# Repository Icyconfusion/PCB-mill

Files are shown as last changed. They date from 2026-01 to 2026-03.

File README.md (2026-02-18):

# PCB-mill
A small cnc machine for milling FR4 pcbs using an arduino UNO. It is also capable of CNC engraving at low Z travels. You could potentially do laser engraving if you added a laser to it.

**Note to reveiwer:** I have exported the assembly as .STEP, but I had trouble so there is a zipped .stl of the assembly just in case the .step doesn't work. Also I am updating my BOM with the current prices (since submission) so it might be slightly different (most are cheaper) from my cart pictures. Thank you :) Also, yes the spindle is the cheapest option (prices are in AUD so 50-60 USD is 75-90 AUD). The spindle I am purchasing also includes PSU.

I created this project as a means to create PCBs quickly at home, removing the time and cost of ordering PCBs online. Now I can make 2 layer PCBs at home on my desk for quick prototyping. It also taught me a few things about routing with power draws. To use the project, you simply stream Gcode to the machine over usb form a computer, and the machine will replicate it.

# **Assembly**


The assembly of the project is made up of a few key components. The idea is a stationary, square base with linear rails making the Y axis. The H frame moves along thiscarrying the X and Z axis. Motion is achieved through leadscrews.

To start assembly, there is the base frame that the whole machine is supported by. 4 2020 300m T slot Aluminium profiles are arranged in a square, with M5 T nuts and 90 degree connectors holding them in place. Two 300mm MGN12 linear rails are attached to the top edge of the profiles using M3 T nuts.


Now onto the H. The H moves back and forth along the linear rails attached before, this is the Y axis. The H moves along the rails by a 3d printed bracket, to attach it to the MGN12H carriage. Use 4 M2 screws to attach each bracket to the carriages, then 4 M5 T nuts to attach profiles to each bracket.





We now have the two pillars of the H. Attach to 2060 profile to the pillars using M5 T nuts and 90 degree connectors. The bottom edge of the 2060 should be roughly 4 cm from the top of the bracket we assembled (Exactness is not needed as Z leveling and the spindle height on the mount will compensate for this). Attach the linear rails as before.


To assemble the gantry, screw on both rear MGN12H carriages, and linear rails. Attach the limit switch and press the bearing into place. Then assemble the spindle plate and slide onto the gantry.




Finally, attach the motor, coupler, nutblock and rod, and then slide onto the H frame. The H frame can now slide onto the base frame rails.



Last steps, attach a bed/spoilboard of wood with M5 T nuts. Screw nutblocks to each Y carriage, then mount all 4 Y axis brackets, and their fixing blocks (plus limit switch on one). Now you can feed the rods through and attach the GT2 gears.


Mount the belt plate, motor and drive gear using M5 T nuts, then attach the pulleys.



Finally, attach the X motor bracket, motor and limit switch. The fixing block attaches to the profile on the other side using the T nuts already installed on it. Now you can feed through the leadscrew and assembly is done.



# **Electronics**
The components required for this project are a PSU, an MCU, a spindle or spindle kit, stepper motors, stepper drivers, and limit switches. For the MCU I decided on an arduino UNO because of its pin availability and GRBL compatibility. To power the UNO, I will use an LM2596 buck converter connected to the VIN pin. The PSU is 24v logic, 200w. Power is introduced to the PCB by screw terminals, and powers the VMOT pin of drivers, and 5v logic through the arduino. The steppers are Nema 17 because of their cheap cost and reliability. Drivers used to control these are A4988, which support 1/16 microstepping (why all MS pins are connected to 5v). The 500w spindle comes as a kit including a mount and dedicated PSU. This kit also has speed control to stop the spindle. I am using standard 3 pin limit switches.

## Schematic

Cirkit designer: https://app.cirkitdesigner.com/project/915723a2-d3f0-4d32-8109-c895c4144bcc


## PCB
The PCB for this project interfaces the power supply, steppers, arduino and endstops. It uses wide traces to deliver power from the PSU screw terminals, and has connectors from leftover pins for future connections.


# **Firmware**
The project uses the GRBL library to command the machine. GRBL is a program that instructs the arduino to respond to G-code, sent by a computer. No modifications to GBRL are required other than tweaking default steps/mm, speed, acceleration etc to the machine. To install, copy the edited firmware folder into Arduino IDE libraries, include it in a sketch, and then flash. **It is installed as a zip.**

# **BOM**

### CAD

|Quantity|Name|Picture|
|---|----|---|
| 1 | Spindle plate |  |
| 1 | Gantry plate |  |
| 1 | X motor bracket |  |
| 2 | Y carriage |  |
| 1 | Y bearing bracket with switch |  |
| 3 | Y bearing bracket |  |
| 1 | Belt plate |  |

### PCB

2 layer PCB that is 127x118mm.


### Parts
3x Nema 17 stepper motor

1x Arduino uno

3x A4988 stepper driver

1x 24v 200w PSU

1x 500w Spindle kit

1x LM2596 Buck converter

3x Limit switch

1x V bit

1x Drill bit

1x End mill

1x Collet

6x 300mm 2020 T slot aluminium profile (can do 4x300mm and 2x 200mm, but 6x300mm ended up being cheaper)

1x 300mm 2060 T slot profile

8x 90 degree connector

42x M5 T nut

42x M5 screw

32x M3 screw

32x M3 T nut

1x 100mm T8x8 Leadscrew

3x 300mm T8x8 leadscrew

2x 100mm MGN12 linear rail (with MGN12H carriage)

4x 300mm MGN12 linear rail (with MGN12H carriage)

4x T8x8 nutblock 2mm pitch

2x 5x8mm shaft coupler

1x 5mm bore GT2 timing gear

2x 8mm bore GT2 timing gear

1x GT2 belt (at least 600mm)

2x Toothed GT2 idle pulley

2x Smooth GT2 idle pulley

4x Leadscrew fixing block

1x 16x8x5 bearing

1x spoilboard (any wooden sheet)

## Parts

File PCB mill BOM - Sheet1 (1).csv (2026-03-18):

Product | Quantity | Description | Supplier | Cost (USD) | Link
Nema 17 | 3 |  | Aliexpress | 27.58 | https://www.aliexpress.com/item/1005008459399126.html?curPageLogUid=vCnLCC6yeYcx
Arduino Uno | 1 |  | Aliexpress | 7.35 | https://www.aliexpress.com/item/1005009166789162.html?curPageLogUid=tjsaISsRPt8N
A4988 | 3 |  | Temu | 6.04 | https://www.temu.com/au/5pcs-a4988-stepper--module-with-heat-sink-compatible-for-3d-printer-cnc-machine-robotics-heavy-duty-stepper-driver-board-low-voltage-o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
PSU | 1 |  | Aliexpress | 19.71 | https://www.aliexpress.com/item/1005008333292020.html?curPageLogUid=3XLdhquhUHAm
Spindle kit | 1 |  | Aliexpress | 57.46 | https://www.aliexpress.com/item/1005010191382404.html?curPageLogUid=LtoxsOxznCte
Buck converter | 1 |  | Aliexpress | 2.75 | https://www.aliexpress.com/item/1005007003796615.html?curPageLogUid=gSlzuXtzWAvK
Limit switch | 3 | I already Have these so do not need funding
Z probe | 1 | Already have this so don't need to purchase
V bit | 1 |  | Aliexpress | 8.24 | https://www.aliexpress.com/item/33058654975.html?curPageLogUid=Qey6XFCZCbFq
Collets | 1 |  | Aliexpress | 5.89 | https://www.aliexpress.com/item/1005007808859713.html?curPageLogUid=pwjcIhmlvNUK
Drill bit | 1 |  | Aliexpress | 3.09 | https://www.aliexpress.com/item/1005004411348630.html?curPageLogUid=OUldsYXfEfkz
End mill | 1 |  | Aliexpress | 1.88 | https://www.aliexpress.com/item/1005003291713022.html?curPageLogUid=ExpGw3ASmdvT
2020 T slot | 6 |  | Temu | 26.04 | https://www.temu.com/au/6pcs-of-300mm-11-8-inch-t-slot-2020-aluminum-profile-extrusion-european-standard-anodized-linear-guide-rail-aluminum-profile-extrusion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
2060 T slot | 1 |  | Aliexpress | 14.02 | https://www.aliexpress.com/item/1005002883217574.html?curPageLogUid=gkx3e2LF0D2x
90 degree bracket | 8 | Already have this so don't need to purchase
M5 T Nuts | 42 |  | Temu | 2.14 | https://www.temu.com/au/50pcs-durable-carbon-steel-t-nuts--m4-m5-sizes-nickel-plated-rust-resistant--for-industrial-aluminum-frame--3d-printers-cnc-routers-id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
M3 T nuts | 32 |  | Temu | 2.67 | https://www.temu.com/au/50pcs-of-2020-series-t-nuts--m4-m5-t-slot-nuts-hammer-fasteners-aluminum-profile-plated-carbon-steel-sliding-t-nuts-g-601099530397912.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
100mm leadscrew | 1 |  | Aliexpress | 3.89 | https://www.aliexpress.com/item/1005006178955178.html?curPageLogUid=c6d8BTDWwVPy
300mm leadscrew | 2 |  | Temu | 11.34 | https://www.temu.com/au/tr8x8-screw-with-t8-nut-trapezoidal-thread-2mm-pitch-4-threads-8mm-suitable-for--axis-of-lcd-dlp-sla-3d-printers-and-cnc-machines-g-60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
300mm leadscrew | 1 |  | Alixpress | 6.92 | https://www.aliexpress.com/item/1005009554037590.html?curPageLogUid=qyEKHqJXyCOE
300mm Linear rail | 4 |  | Aliexpress | 57.75 | https://www.aliexpress.com/item/1000007480470.html?curPageLogUid=xv41WxawscEY
100mm Linear rail | 2 |  | Aliexpress | 17.16 | https://www.aliexpress.com/item/1000007480470.html?curPageLogUid=xv41WxawscEY
Nut block | 4 |  | Aliexpress | 5.88 | https://www.aliexpress.com/item/1005007569770523.html?curPageLogUid=jOi7LGcCxd76
Shaft coupler | 2 |  | Aliexpress | 4.13 | https://www.aliexpress.com/item/1005007287308755.html?curPageLogUid=RoRBVjjHc6Wq
5mm Bore GT2 Drive gear | 1 |  | Aliexpress | 1.34 | https://www.aliexpress.com/item/32781681772.html?curPageLogUid=3ezKj0Eq3S47
8mm bore GT2 drive gear | 2 |  | Aliexpress | 1.3 | https://www.aliexpress.com/item/32781681772.html?curPageLogUid=3ezKj0Eq3S47
GT2 belt | 1 |  | Aliexpress | 1.84 | https://www.aliexpress.com/item/1005003301991078.html?curPageLogUid=Z2PgWSwreJ6X
Gt2 idle pulleys | 4 | 2 with teeth, 2 without | Aliexpress | 4.83 | https://www.aliexpress.com/item/32817328238.html?curPageLogUid=Ry0fcXbuAR7Z
Leadscrew fixing block | 4 |  | Aliexpress | 7.4 | https://www.aliexpress.com/item/1005009834401051.html?curPageLogUid=naPMBq5fiutL
Bearing | 1 |  | Aliexpress | 3.56 | https://www.aliexpress.com/item/1005004937963687.html?curPageLogUid=k503JPjwGYyO
 |  |  |  | 312.2

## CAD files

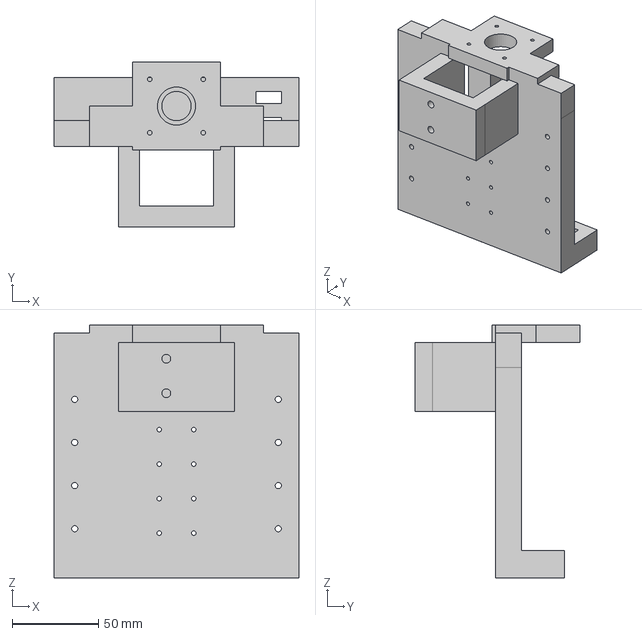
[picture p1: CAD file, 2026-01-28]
CAD/Plate Gantry.step
142.0 x 95.6 x 146.5 mm

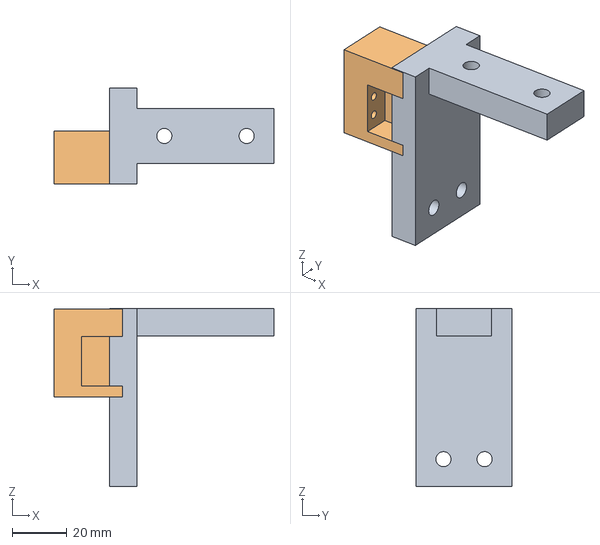
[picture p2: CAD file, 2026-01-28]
CAD/Y bearing bracket with switch.step
80.2 x 35.0 x 65.0 mm

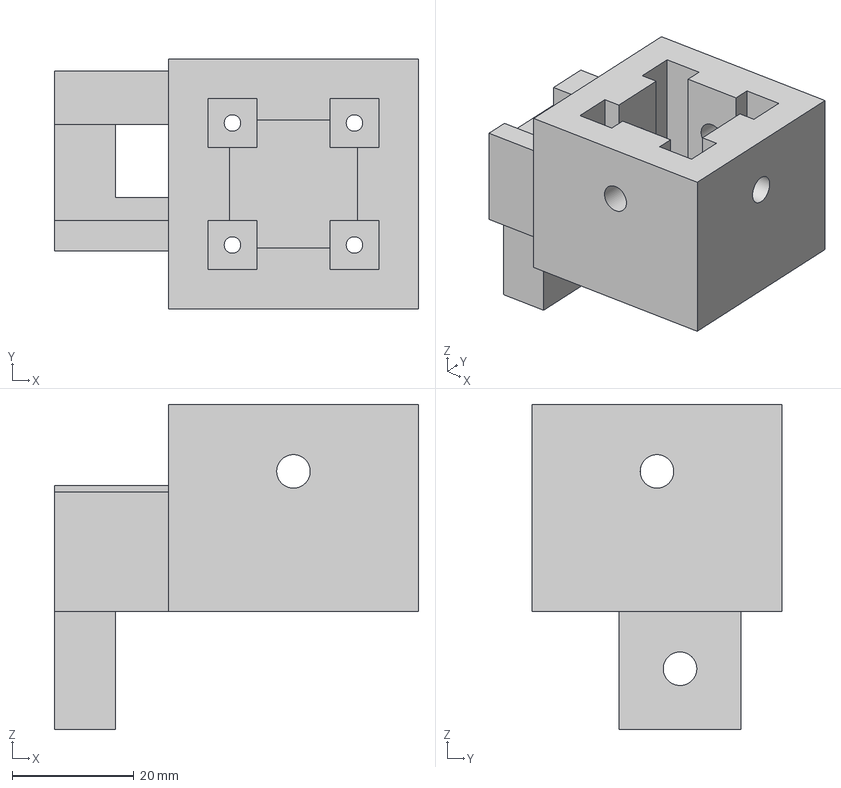
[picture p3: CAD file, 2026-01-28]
CAD/Y carriage.step
59.7 x 41.0 x 53.4 mm

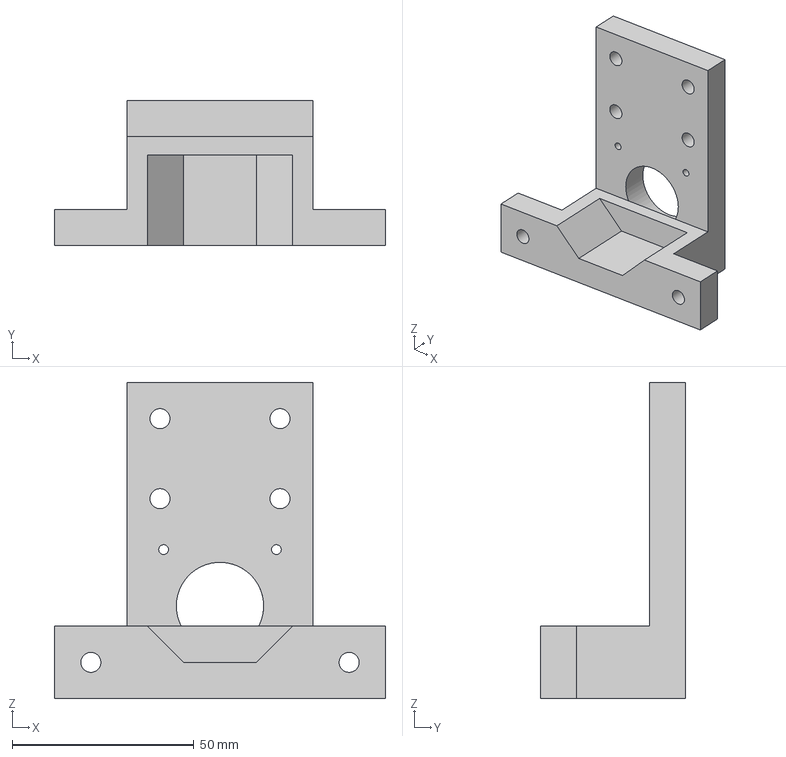
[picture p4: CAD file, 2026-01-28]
CAD/Belt plate.step
91.0 x 40.0 x 87.0 mm

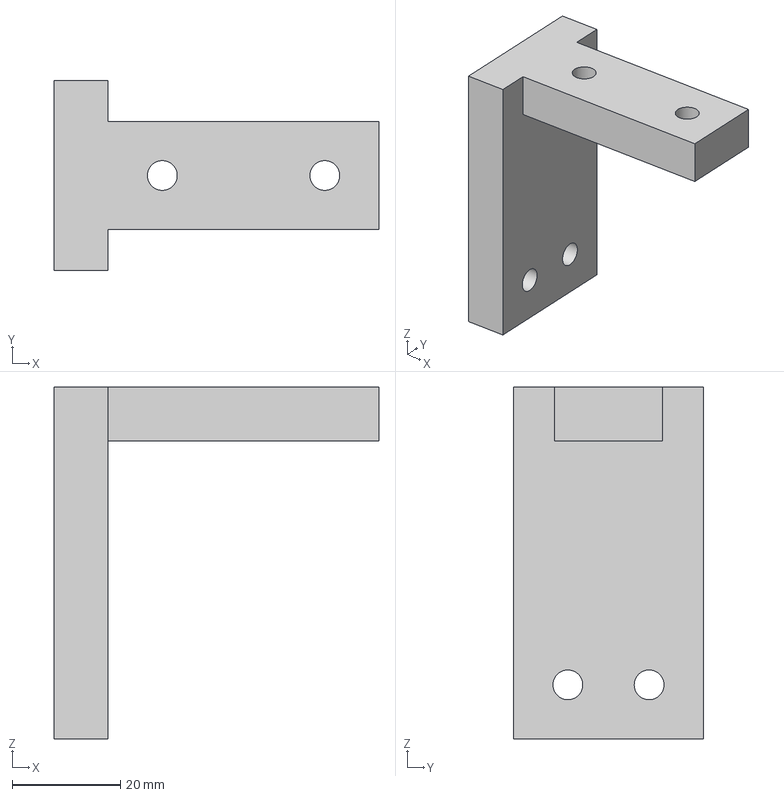
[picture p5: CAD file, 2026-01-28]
CAD/Y bearing bracket.step
60.0 x 35.0 x 65.0 mm

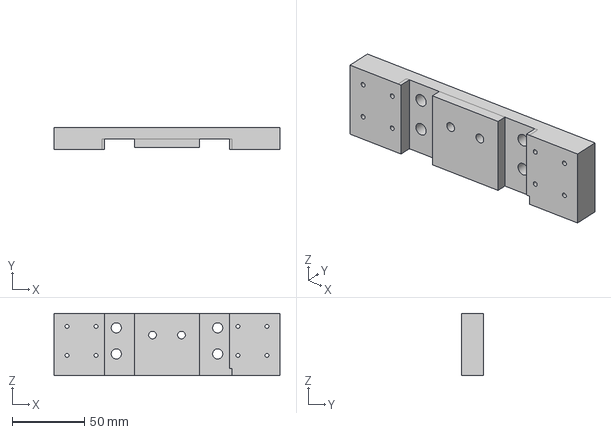
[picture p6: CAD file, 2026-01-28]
CAD/Spindle plate.step
156.0 x 15.3 x 43.0 mm

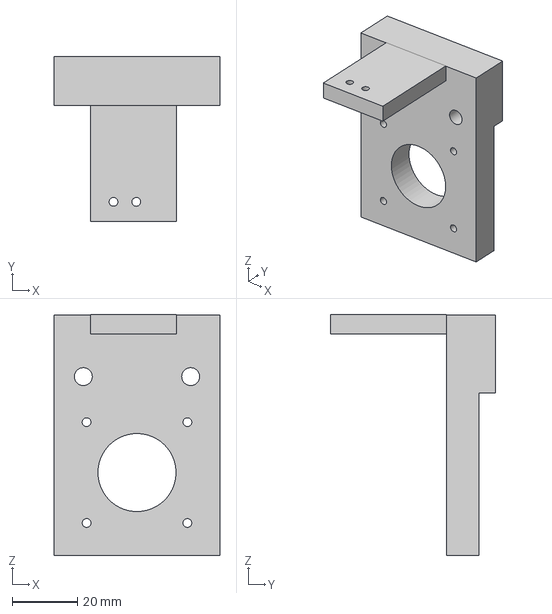
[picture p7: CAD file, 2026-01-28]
CAD/X motor bracket.step
51.0 x 50.7 x 74.1 mm

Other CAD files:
Assembly/Assembly.step

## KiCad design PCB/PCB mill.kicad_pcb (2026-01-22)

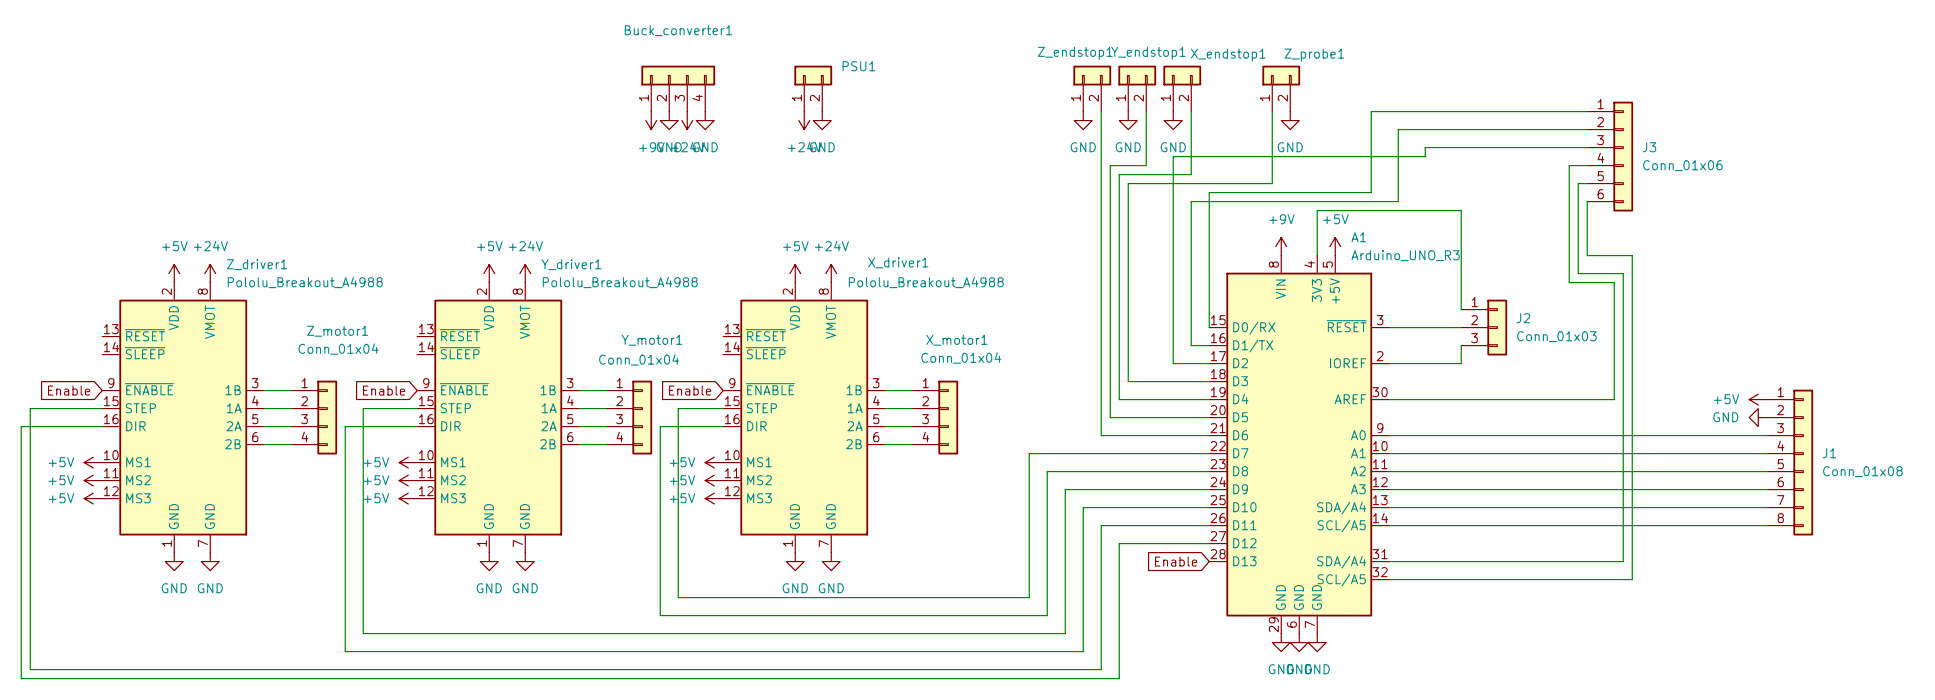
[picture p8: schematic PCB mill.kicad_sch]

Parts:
A1: Arduino_UNO_R3
Buck_converter1: Conn_01x04; PinHeader_1x04_P2.54mm_Vertical
J1: Conn_01x08; PinHeader_1x08_P2.54mm_Vertical
J2: Conn_01x03; PinHeader_1x03_P2.54mm_Vertical
J3: Conn_01x06; PinHeader_1x06_P2.54mm_Vertical
PSU1: Conn_01x02; Wuerth_691311400102_P7.62mm
X_driver1: Pololu_Breakout_A4988; Pololu_Breakout-16_15.2x20.3mm
X_endstop1: Conn_01x02; PinHeader_1x02_P2.54mm_Vertical
X_motor1: Conn_01x04; PinHeader_1x04_P2.54mm_Vertical
Y_driver1: Pololu_Breakout_A4988; Pololu_Breakout-16_15.2x20.3mm
Y_endstop1: Conn_01x02; PinHeader_1x02_P2.54mm_Vertical
Y_motor1: Conn_01x04; PinHeader_1x04_P2.54mm_Vertical
Z_driver1: Pololu_Breakout_A4988; Pololu_Breakout-16_15.2x20.3mm
Z_endstop1: Conn_01x02; PinHeader_1x02_P2.54mm_Vertical
Z_motor1: Conn_01x04; PinHeader_1x04_P2.54mm_Vertical
Z_probe1: Conn_01x02; PinHeader_1x02_P2.54mm_Vertical

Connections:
+5V: A1.5 (+5V), J1.1, X_driver1.2 (VDD), X_driver1.10 (MS1), X_driver1.11 (MS2), X_driver1.12 (MS3), Y_driver1.2 (VDD), Y_driver1.10 (MS1), Y_driver1.11 (MS2), Y_driver1.12 (MS3), Z_driver1.2 (VDD), Z_driver1.10 (MS1), Z_driver1.11 (MS2), Z_driver1.12 (MS3)
+9V: A1.8 (VIN), Buck_converter1.1
+24V: Buck_converter1.3, PSU1.1, X_driver1.8 (VMOT), Y_driver1.8 (VMOT), Z_driver1.8 (VMOT)
Enable: A1.28 (D13), X_driver1.9 (~ENABLE), Y_driver1.9 (~ENABLE), Z_driver1.9 (~ENABLE)
GND: A1.6 (GND), A1.7 (GND), A1.29 (GND), Buck_converter1.2, Buck_converter1.4, J1.2, PSU1.2, X_driver1.1 (GND), X_driver1.7 (GND), X_endstop1.1, Y_driver1.1 (GND), Y_driver1.7 (GND), Y_endstop1.1, Z_driver1.1 (GND), Z_driver1.7 (GND), Z_endstop1.1, Z_probe1.2
unnamed: A1.4 (3V3), J2.1
unnamed: A1.9 (A0), J1.3
unnamed: A1.10 (A1), J1.4
unnamed: A1.11 (A2), J1.5
unnamed: A1.12 (A3), J1.6
unnamed: A1.30 (AREF), J3.4
unnamed: A1.15 (D0/RX), J3.1
unnamed: A1.16 (D1/TX), J3.2
unnamed: A1.17 (D2), J3.3
unnamed: A1.18 (D3), Z_probe1.1
unnamed: A1.19 (D4), X_endstop1.2
unnamed: A1.20 (D5), Y_endstop1.2
unnamed: A1.21 (D6), Z_endstop1.2
unnamed: A1.22 (D7), X_driver1.15 (STEP)
unnamed: A1.23 (D8), X_driver1.16 (DIR)
unnamed: A1.24 (D9), Y_driver1.15 (STEP)
unnamed: A1.25 (D10), Y_driver1.16 (DIR)
unnamed: A1.26 (D11), Z_driver1.15 (STEP)
unnamed: A1.27 (D12), Z_driver1.16 (DIR)
unnamed: A1.2 (IOREF), J2.3
unnamed: A1.3 (~RESET), J2.2
unnamed: A1.13 (SDA/A4), J1.7
unnamed: A1.14 (SCL/A5), J1.8
unnamed: A1.31 (SDA/A4), J3.5
unnamed: A1.32 (SCL/A5), J3.6
unnamed: X_driver1.4 (1A), X_motor1.2
unnamed: X_driver1.3 (1B), X_motor1.1
unnamed: X_driver1.5 (2A), X_motor1.3
unnamed: X_driver1.6 (2B), X_motor1.4
unnamed: Y_driver1.4 (1A), Y_motor1.2
unnamed: Y_driver1.3 (1B), Y_motor1.1
unnamed: Y_driver1.5 (2A), Y_motor1.3
unnamed: Y_driver1.6 (2B), Y_motor1.4
unnamed: Z_driver1.4 (1A), Z_motor1.2
unnamed: Z_driver1.3 (1B), Z_motor1.1
unnamed: Z_driver1.5 (2A), Z_motor1.3
unnamed: Z_driver1.6 (2B), Z_motor1.4

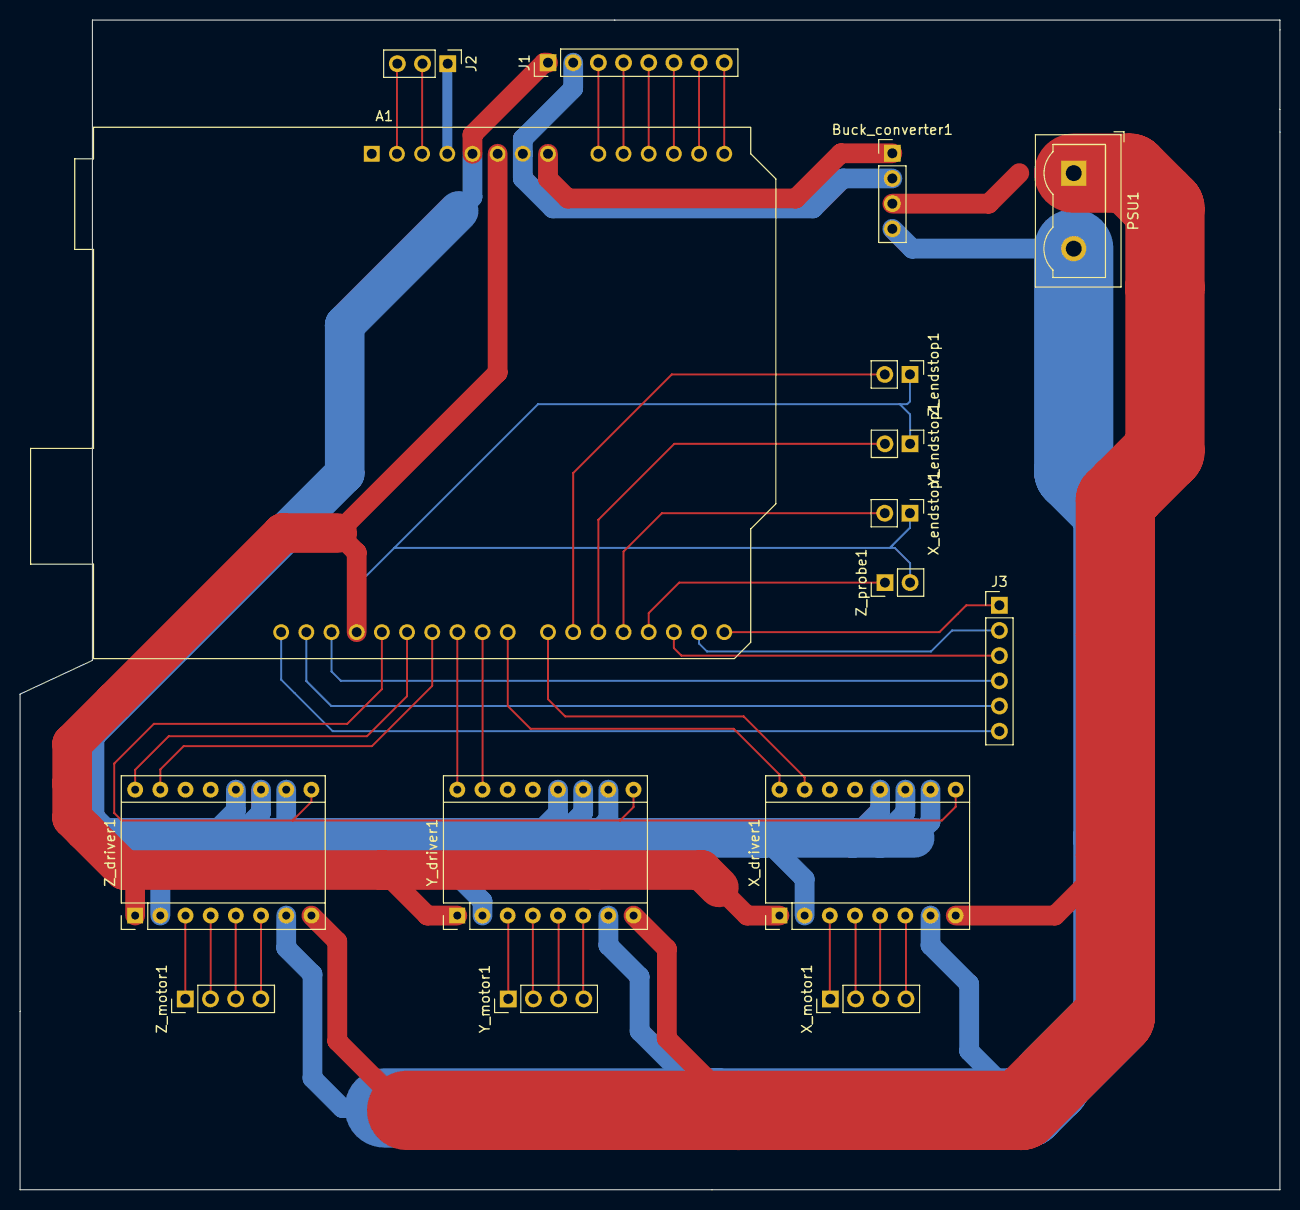
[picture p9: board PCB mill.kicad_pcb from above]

Board: 2 copper layers, 127.1 x 118.0 mm, 16 parts (0 on the bottom side), 42 nets.

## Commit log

2026-01-22 Update and rename PCB mill.kicad_pcb to PCB/PCB mill.kicad_pcb
    [PCB mill.kicad_pcb]
2026-01-22 Rename PCB mill.kicad_prl to PCB/PCB mill.kicad_prl
2026-01-22 Rename PCB mill.kicad_pro to PCB/PCB mill.kicad_pro
2026-01-22 Update and rename PCB mill.kicad_sch to PCB/PCB mill.kicad_sch
    [PCB mill.kicad_sch]
2026-01-28 Update and rename Belt plate.step to CAD/Belt plate.step
    [Belt plate.step]
2026-01-28 Update and rename Plate Gantry.step to CAD/Plate Gantry.step
    [Plate Gantry.step]
2026-01-28 Update and rename Spindle plate.step to CAD/Spindle plate.step
    [Spindle plate.step]
2026-01-28 Update and rename X motor bracket.step to CAD/X motor bracket.step
    [X motor bracket.step]
2026-01-28 Update and rename Y bearing bracket with switch.step to CAD/Y bearing bracket with switch.step
    [Y bearing bracket with switch.step]
2026-01-28 Update and rename Y bearing bracket.step to CAD/Y bearing bracket.step
    [Y bearing bracket.step]
2026-01-28 Update and rename Y carriage.step to CAD/Y carriage.step
    [Y carriage.step]
2026-01-28 Update and rename Assembly.f3z to Assembly.f3z
    [Assembly.f3z]
